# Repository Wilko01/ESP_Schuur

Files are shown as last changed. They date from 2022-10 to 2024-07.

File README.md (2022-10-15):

# Fan Shed and door contacts shed and gate
This ESP32 controls the door contacts of the shed and gate and the fan of the shed to reduce the humidity in the shed.

## Description and operation instructions
The fan is turned on when a certain humidity is detected and turned off when it is below another humidity value. Opening or closing the shed door has impact as with an open door it is not logical to run the fan. Hence opening the door will immediately shut down the fan. The fan is controlled via different levels where at lower humidity levels the fan runs at a lower speed and when the hunidity level is high the fan runs at a higher speed. The fan is also turned on when the temperature is very high. The logic is running on the ESP32. To be able to override the logic there is an override variable which enables remote control and bypasing the ESP32 fan control.

 ## Technical description
The PWM fan is controlled via the PWM signal coming from the ESP32. The ESP32 is running ESPHOME and connected to Home Assistant. The sensor for the humidity is included in this module, the sensors of the shed door and the gate door are connected to this ESP32, but they only report to Home Assistant where the door sensors can be used with logic in NodeRed.
Tip: 
- When placing the reed contact into the bracket, make sure that the orientation is optimized for a magnet!

### Parts
1 x ESP32

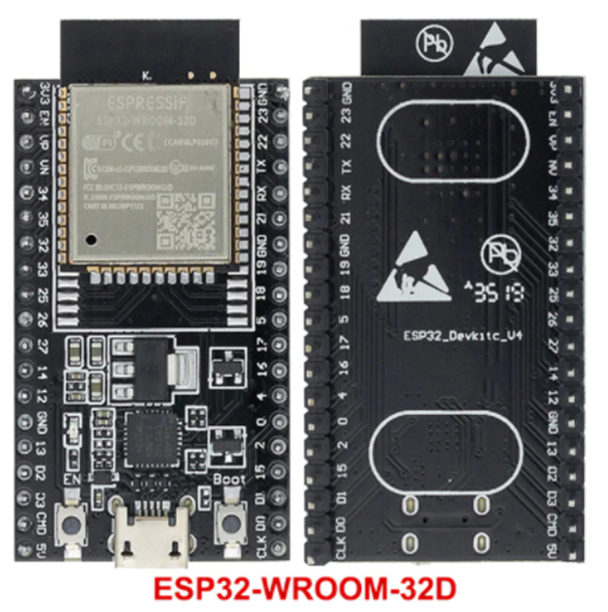
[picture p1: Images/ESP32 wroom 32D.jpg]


1 x DHT22 or AM2302

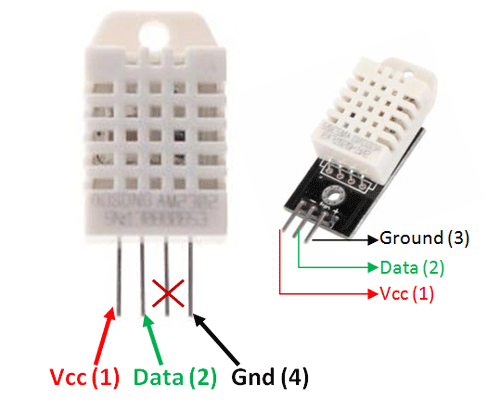
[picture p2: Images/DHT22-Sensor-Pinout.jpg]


1 x DHT22 or AM2302 vs DHT11

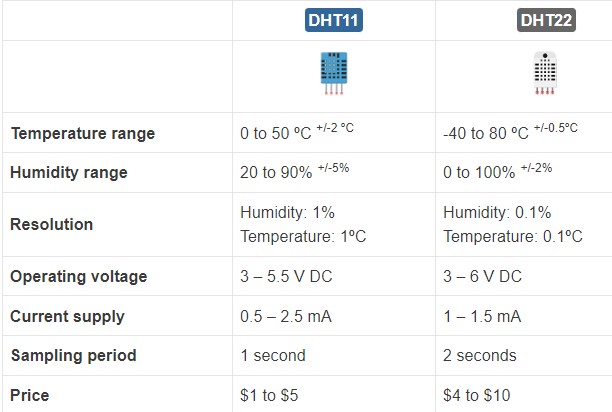
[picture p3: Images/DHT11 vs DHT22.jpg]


2 x Reed contact



1 x Fan NO NF-S12B 1200P Noctua NF-S12B redux-1200 PWM, 120mm

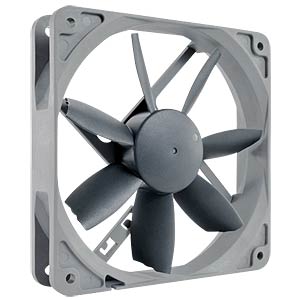
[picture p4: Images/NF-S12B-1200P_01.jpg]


Fan pinout pinout

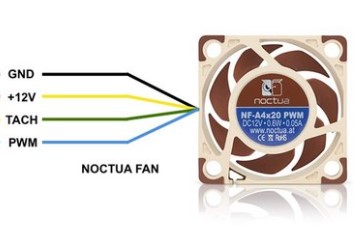
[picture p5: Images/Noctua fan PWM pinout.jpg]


1 x Mini360 DC- DC buck converter

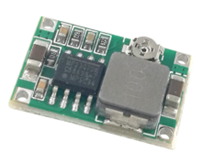
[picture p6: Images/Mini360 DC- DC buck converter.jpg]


Resistors
1 x 180
3 x 1k
1 x 4k7

1 x 12V DC adapter

### Schematic overview
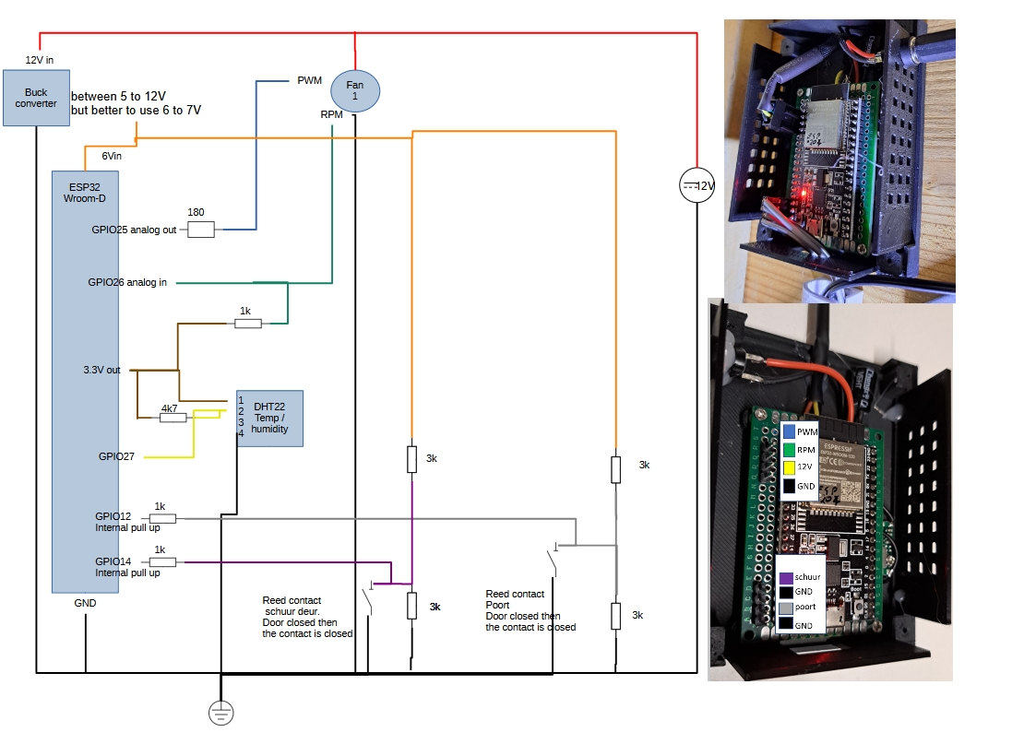
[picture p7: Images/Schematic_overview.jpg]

 
Connector connections overview

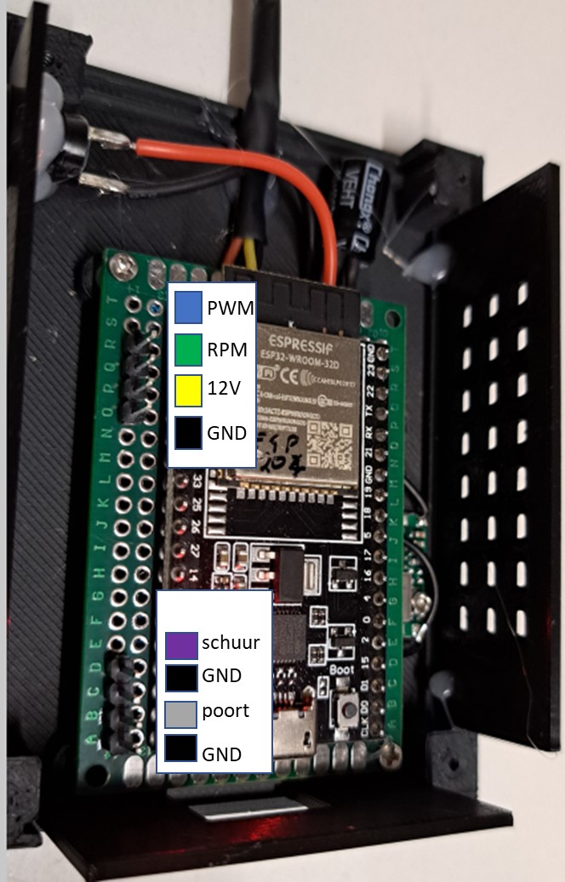
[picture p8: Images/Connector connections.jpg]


•	Power the circuit only via 12V and run code updates via OTA and ESPHOME.

### ESPHOME Configuration
### ESPHome Configuration in Home Assistant
Create a new ESPHOME device with this code:
### Code
[Code in ESPHOME](code.vbs)

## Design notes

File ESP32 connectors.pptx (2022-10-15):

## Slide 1

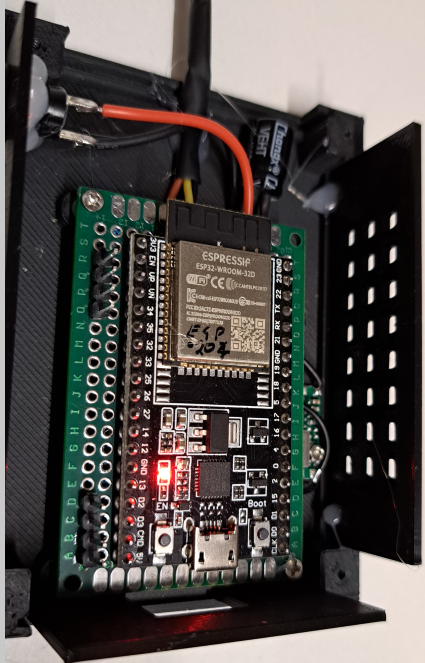
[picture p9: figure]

PWM

RPM

12V

GND

schuur

GND

poort

GND

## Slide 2

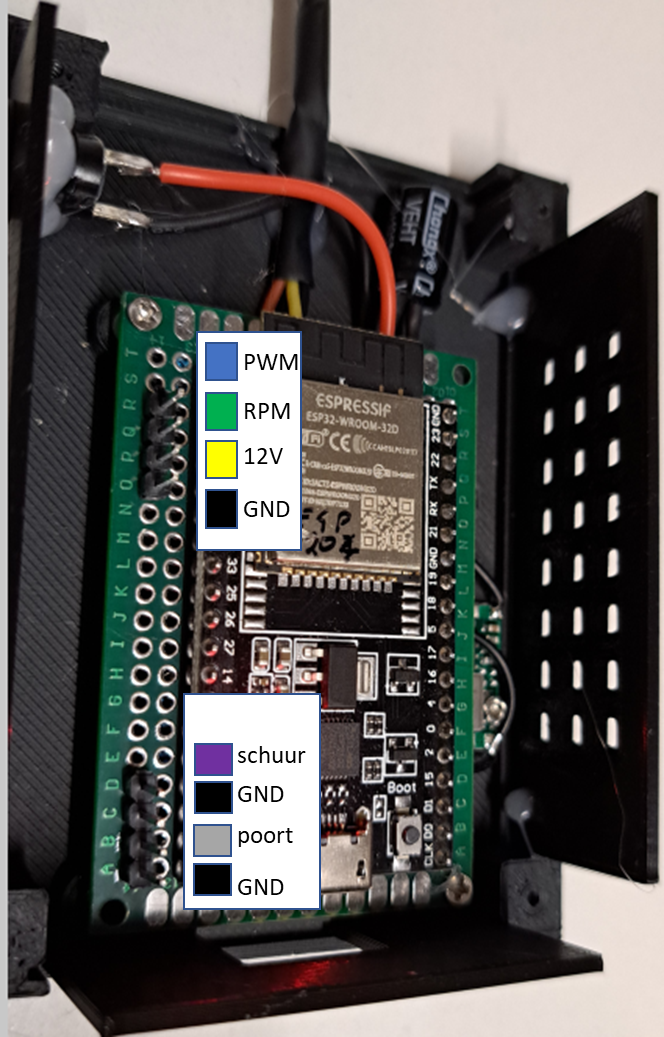
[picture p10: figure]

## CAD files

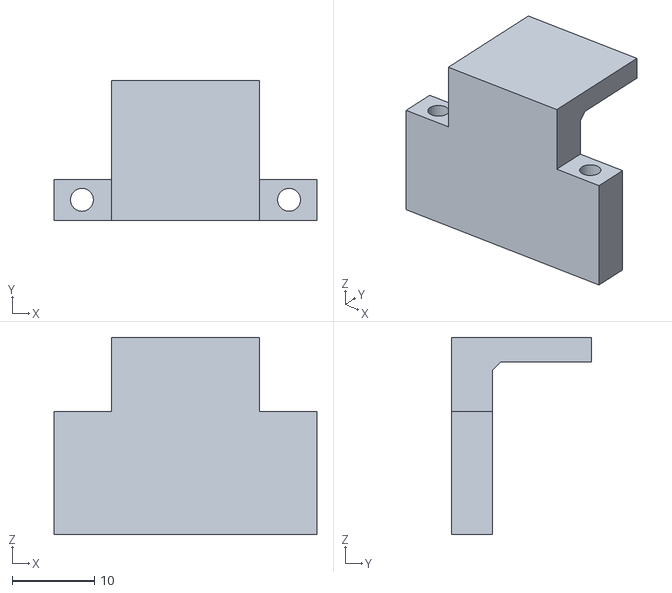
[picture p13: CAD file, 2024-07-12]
3D_Printer_Files/Switch bump 01.stl
32.0 x 17.0 x 24.0

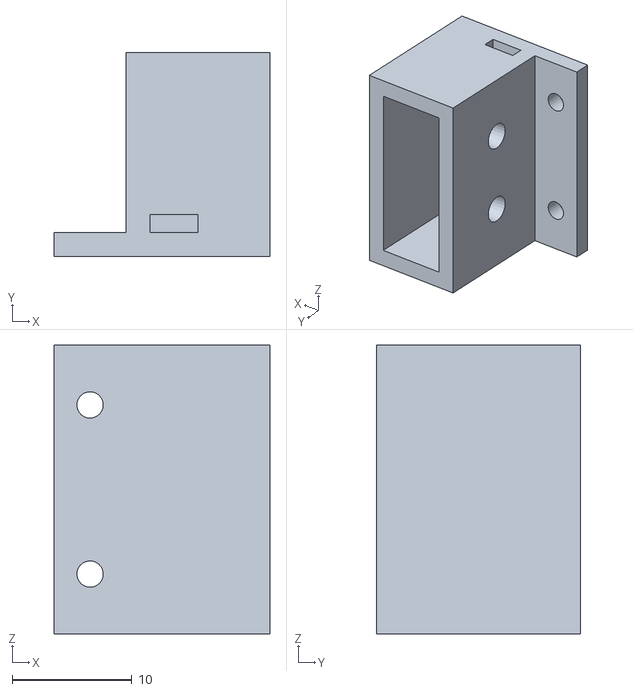
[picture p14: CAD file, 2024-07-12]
3D_Printer_Files/Switch holder 01.stl
18.0 x 17.0 x 24.1

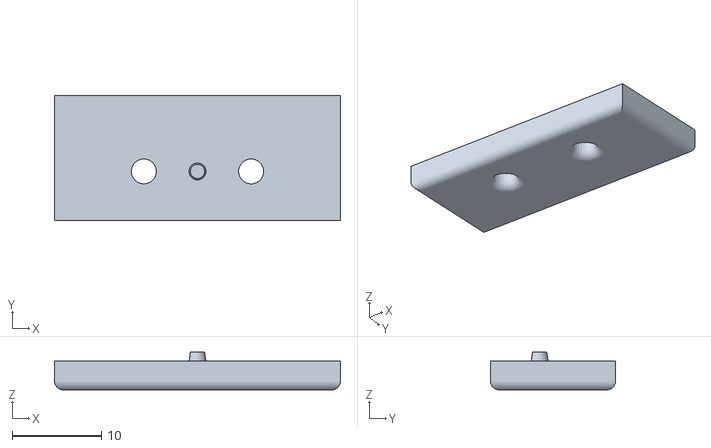
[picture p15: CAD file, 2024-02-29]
3D_Printer_Files/Fan shed - Reed contact top with round edges 02.stl
32.0 x 14.0 x 4.25

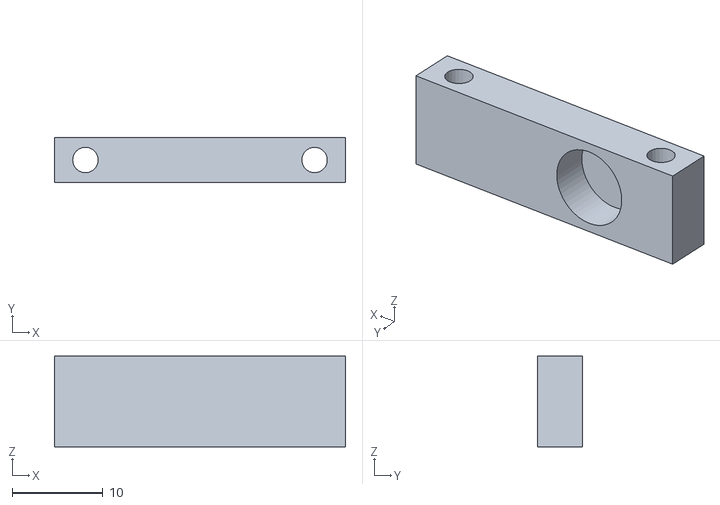
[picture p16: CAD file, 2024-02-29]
3D_Printer_Files/Fan shed magnet holder 01.stl
32.0 x 5.00 x 10.0

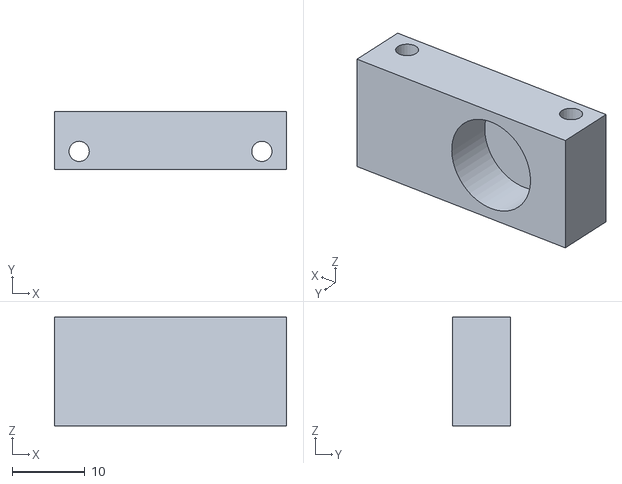
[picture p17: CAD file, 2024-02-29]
3D_Printer_Files/Fan shed magnet holder large magnet 01.stl
32.0 x 8.00 x 15.0

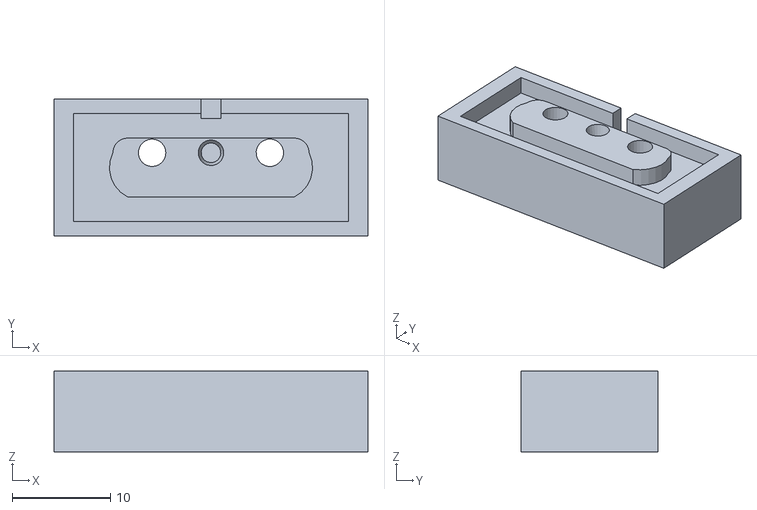
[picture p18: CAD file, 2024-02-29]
3D_Printer_Files/Fan shed - Reed contact bottom 02.stl
32.0 x 14.0 x 8.25

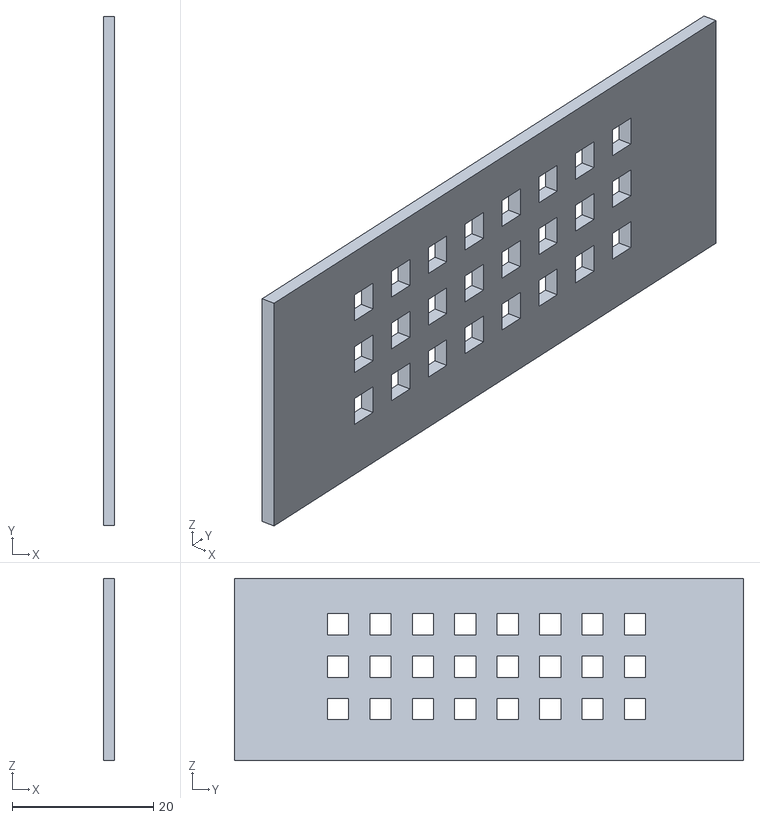
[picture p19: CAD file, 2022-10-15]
3D_Printer_Files/Fan shed side right 01.stl
1.50 x 72.0 x 25.8

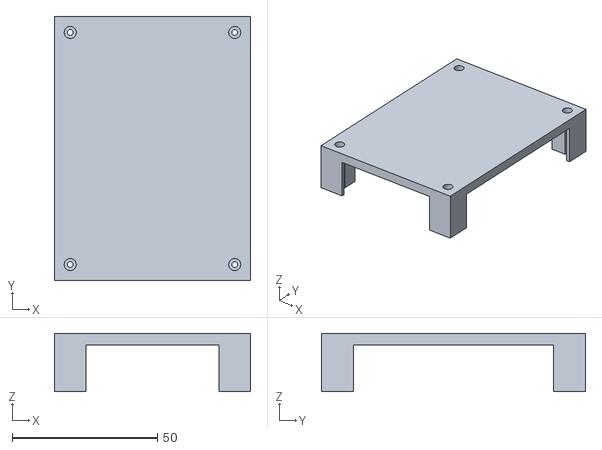
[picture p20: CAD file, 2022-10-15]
3D_Printer_Files/Fan shed cover plate 01.stl
67.7 x 91.0 x 20.0

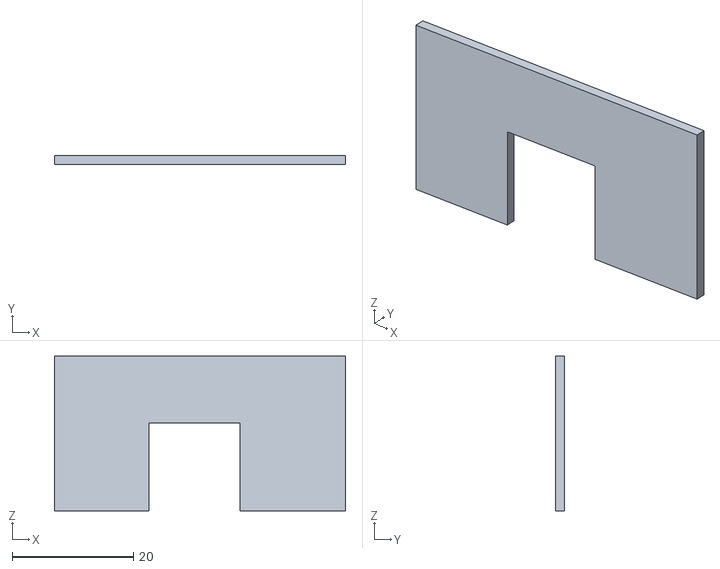
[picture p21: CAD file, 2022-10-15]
3D_Printer_Files/Fan shed side bottom 01.stl
48.0 x 1.50 x 25.5

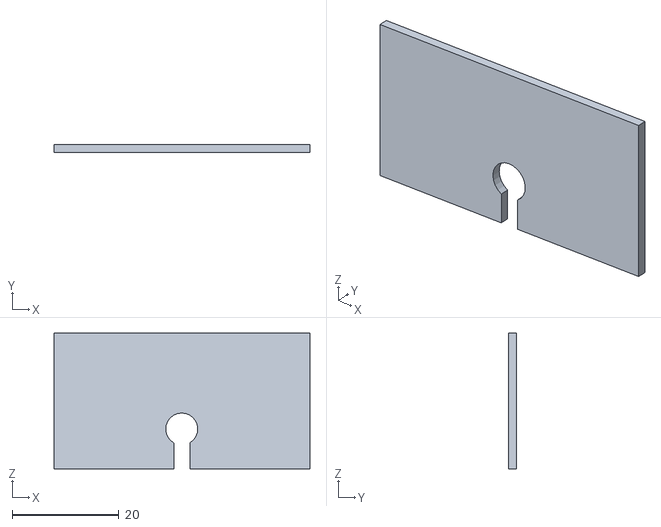
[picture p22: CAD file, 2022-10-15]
3D_Printer_Files/Fan shed side top 01.stl
48.0 x 1.50 x 25.5

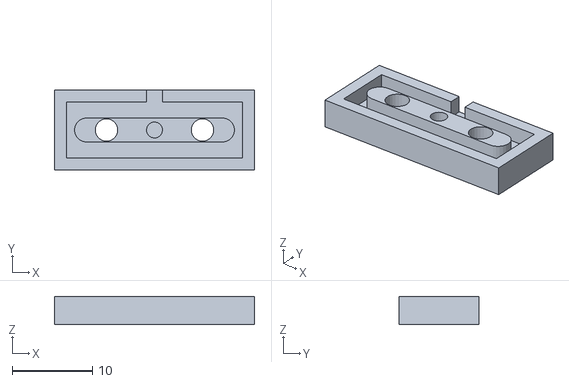
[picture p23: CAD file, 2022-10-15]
3D_Printer_Files/Fan shed - Reed contact bottom.stl
25.0 x 10.0 x 3.50

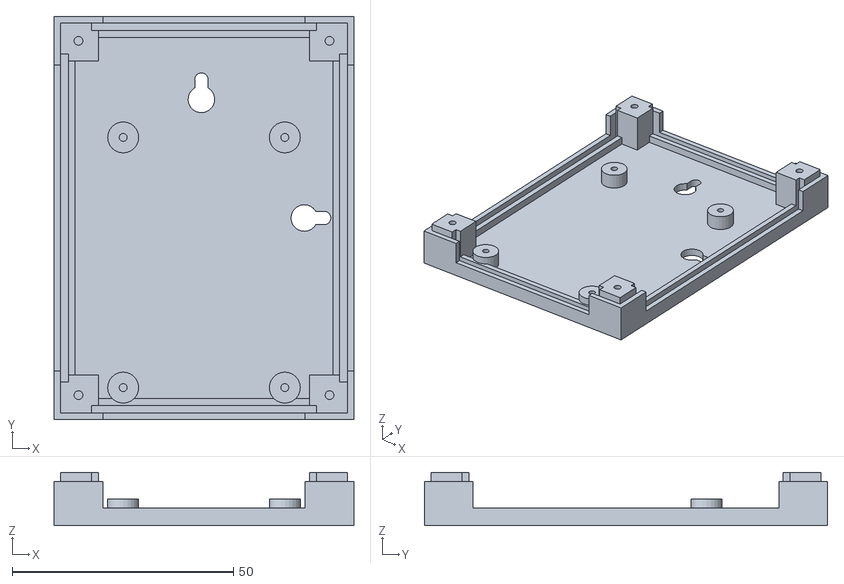
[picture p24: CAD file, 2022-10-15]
3D_Printer_Files/Fan shed bottom plate 01.stl
67.7 x 91.0 x 12.0

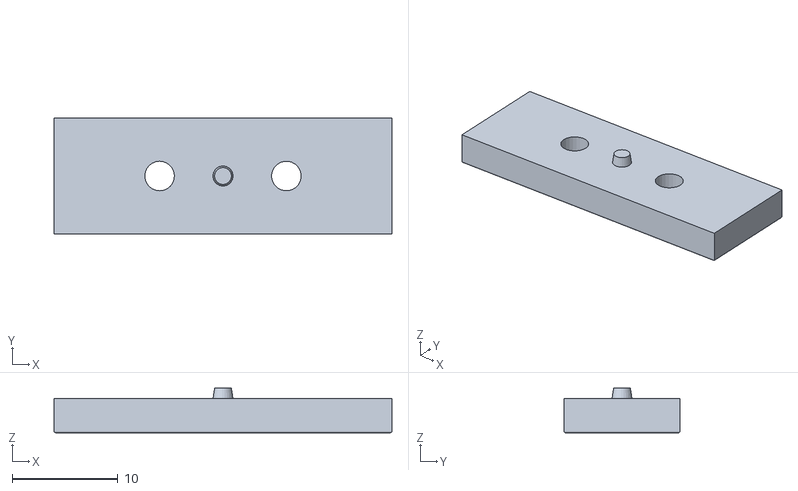
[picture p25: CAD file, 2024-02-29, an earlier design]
3D_Printer_Files/Old/Fan shed - Reed contact top with round edges 01.stl
32.0 x 11.0 x 4.25

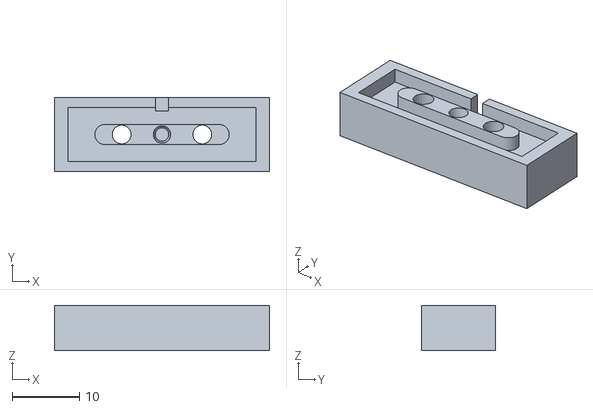
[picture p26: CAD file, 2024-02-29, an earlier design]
3D_Printer_Files/Old/Fan shed - Reed contact bottom 01.stl
32.0 x 11.0 x 6.75

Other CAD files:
3D_Printer_Files/Fan shed side left 01.stl
3D_Printer_Files/Fan shed 03.skp
3D_Printer_Files/Old/Fan shed 01.skp
3D_Printer_Files/Old/Fan shed 02.skp

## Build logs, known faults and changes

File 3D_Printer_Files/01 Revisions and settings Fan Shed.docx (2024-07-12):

# Print settings:

- Print material: PLA
- Rotation of the objects: No comment.
- Support: No
- Skirt, brim: Skirt.
- Infill: 20%

# Additional instructions

- None

# Materials needed

- PLA
- 1 x Bolt M2.5 x 20
- 1 x nuts M2.5

# Log history

# Version 0.3

- The reed contact was not stable, especially not by cold weather around 1’C
- Create a ‘switch holder 01’ and a ‘switch bump 01’ to let the switch wheel run into

# Version 0.2

- Used a larger magnet
- Moved the position of the reed contact to have a closer contact with the magnet

# Version 0.1

- First release

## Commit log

2023-08-19 Added restart button
2023-10-08 added pull up resistors
2024-02-29 update pull up code
    [Fan shed - Reed contact bottom 01.stl, Fan shed - Reed contact bottom 02.stl, Fan shed - Reed contact top 01.stl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]
